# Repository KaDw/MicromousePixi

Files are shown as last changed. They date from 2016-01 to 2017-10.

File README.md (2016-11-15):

# Micromouse Pixi #
	
|  |  |
| ----- | ----- |
| Width | 74mm  |
| Length  | 88mm  |
| Weight  | |
| Wheels  | 3D printed wheels + MZT-302-30 tyres  |
| Microcontroller  | STM32F405RGT6  |
| Motor/Encoder  | Pololu 10:1 HPCB 3000 obr/min + AS5304 encoders  |
| Battery  | Li-Pol Dualsky 7.4V 150mAh 20C  |
| Motor Driver  | TB6612  |
| Sensor | TEFT4300 + SFH4545 X 6  |
| Gyro | FXAS21002C  |

PCB



### Development tools ###

* STM32CubeMX Version 4.17.0
* HAL Libraries - FW_F4 V1.13.1
* Keil uVision 5.21a
* EagleCAD 7.2
* Autodesk Inventor 2016

Development tools can downloaded [here](https://drive.google.com/open?id=0B6SlddUSFtelRTBFR0EwWk1qT1k)

### Setup ###

* CubeMX setup
You can get HAL libraries by going to Help->Install New Libraries->Firmware PAckage for Family STM32F4.
...

### Who do I talk to? ###

* Karol Trzciński 
* Karol Dworakowski karol1dw@gmail.com

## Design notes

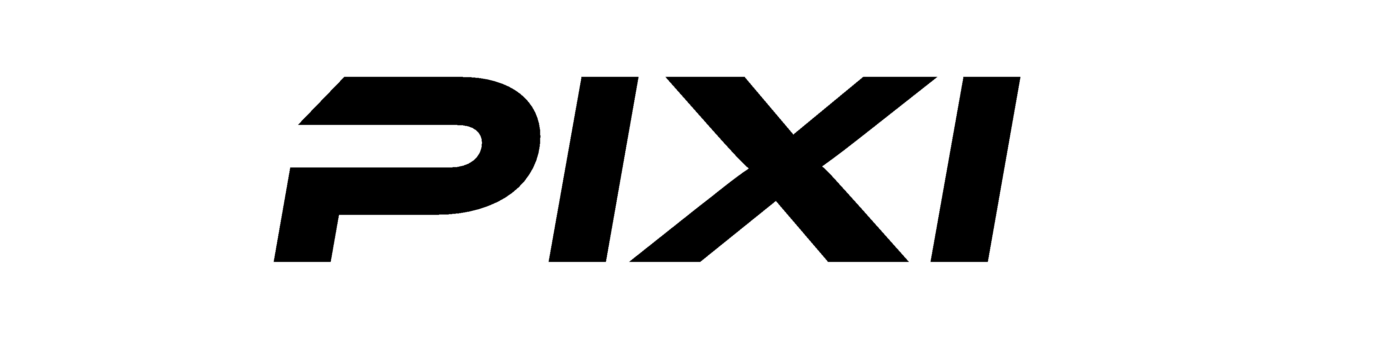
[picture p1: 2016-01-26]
hardware/font/pixi.bmp

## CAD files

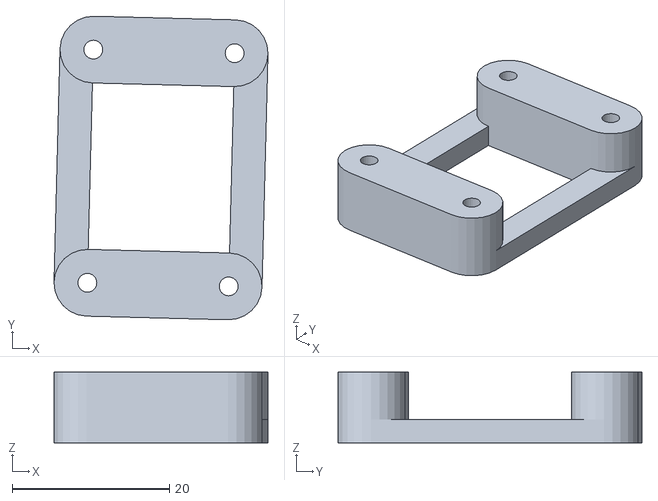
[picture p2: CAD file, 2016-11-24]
hardware/modele/spacer.stl
27.3 x 38.6 x 9.00

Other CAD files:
hardware/modele/wheel.ipt

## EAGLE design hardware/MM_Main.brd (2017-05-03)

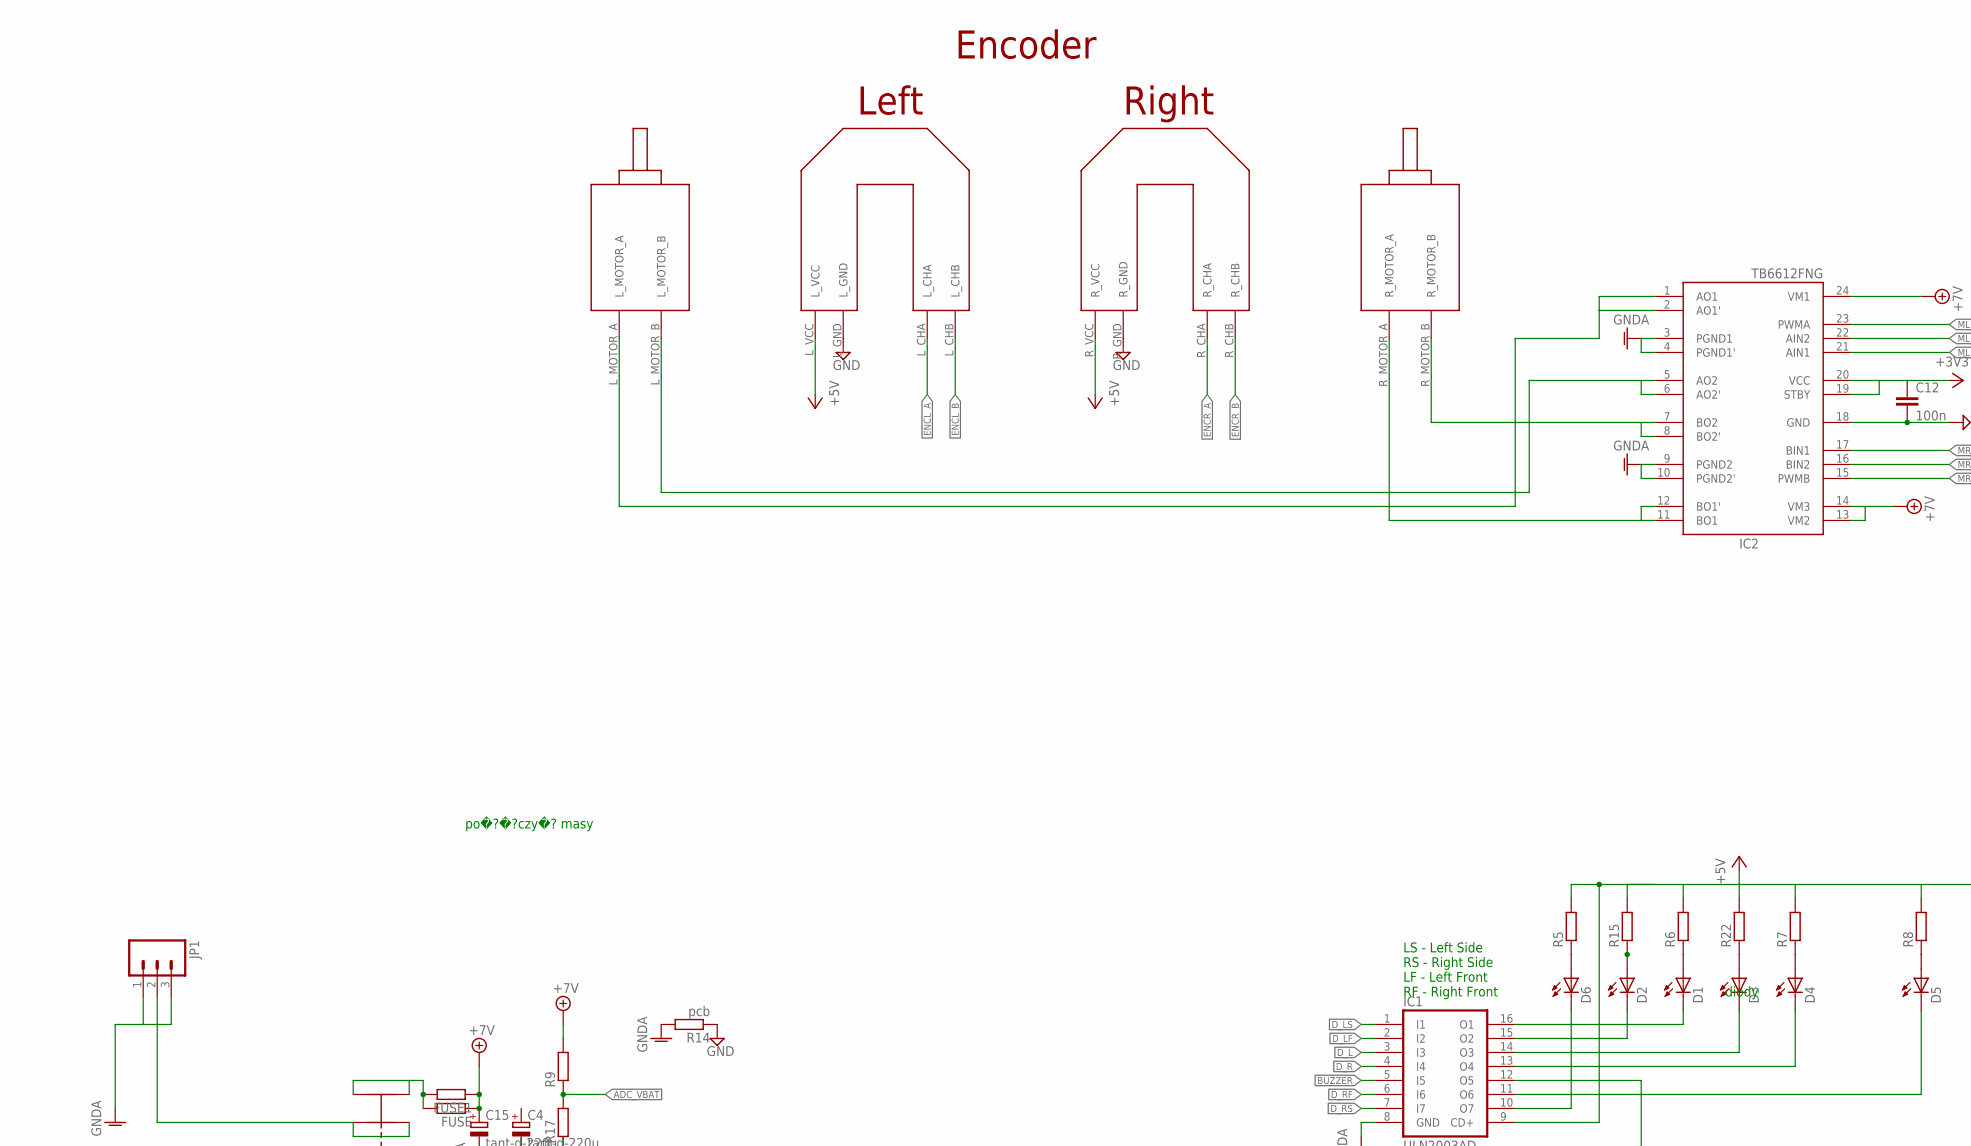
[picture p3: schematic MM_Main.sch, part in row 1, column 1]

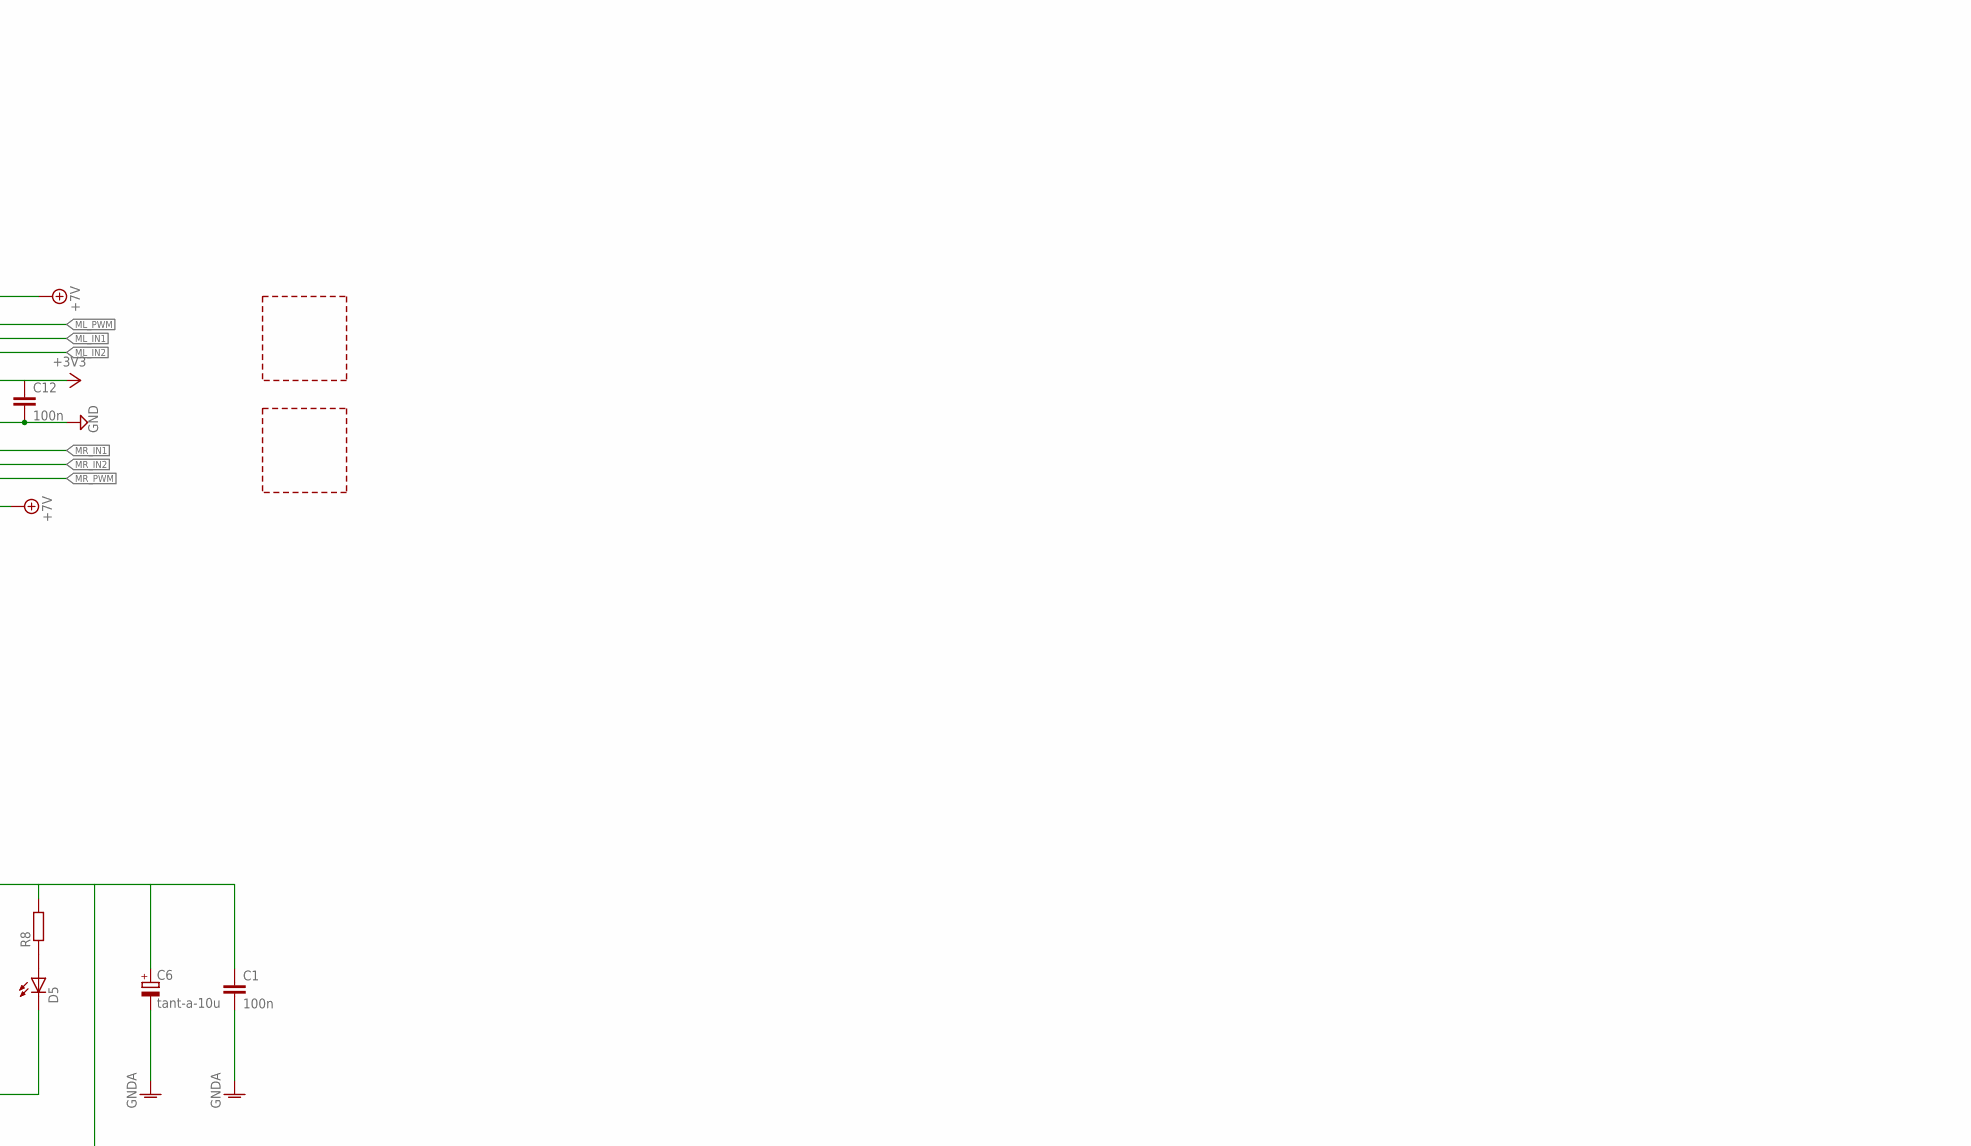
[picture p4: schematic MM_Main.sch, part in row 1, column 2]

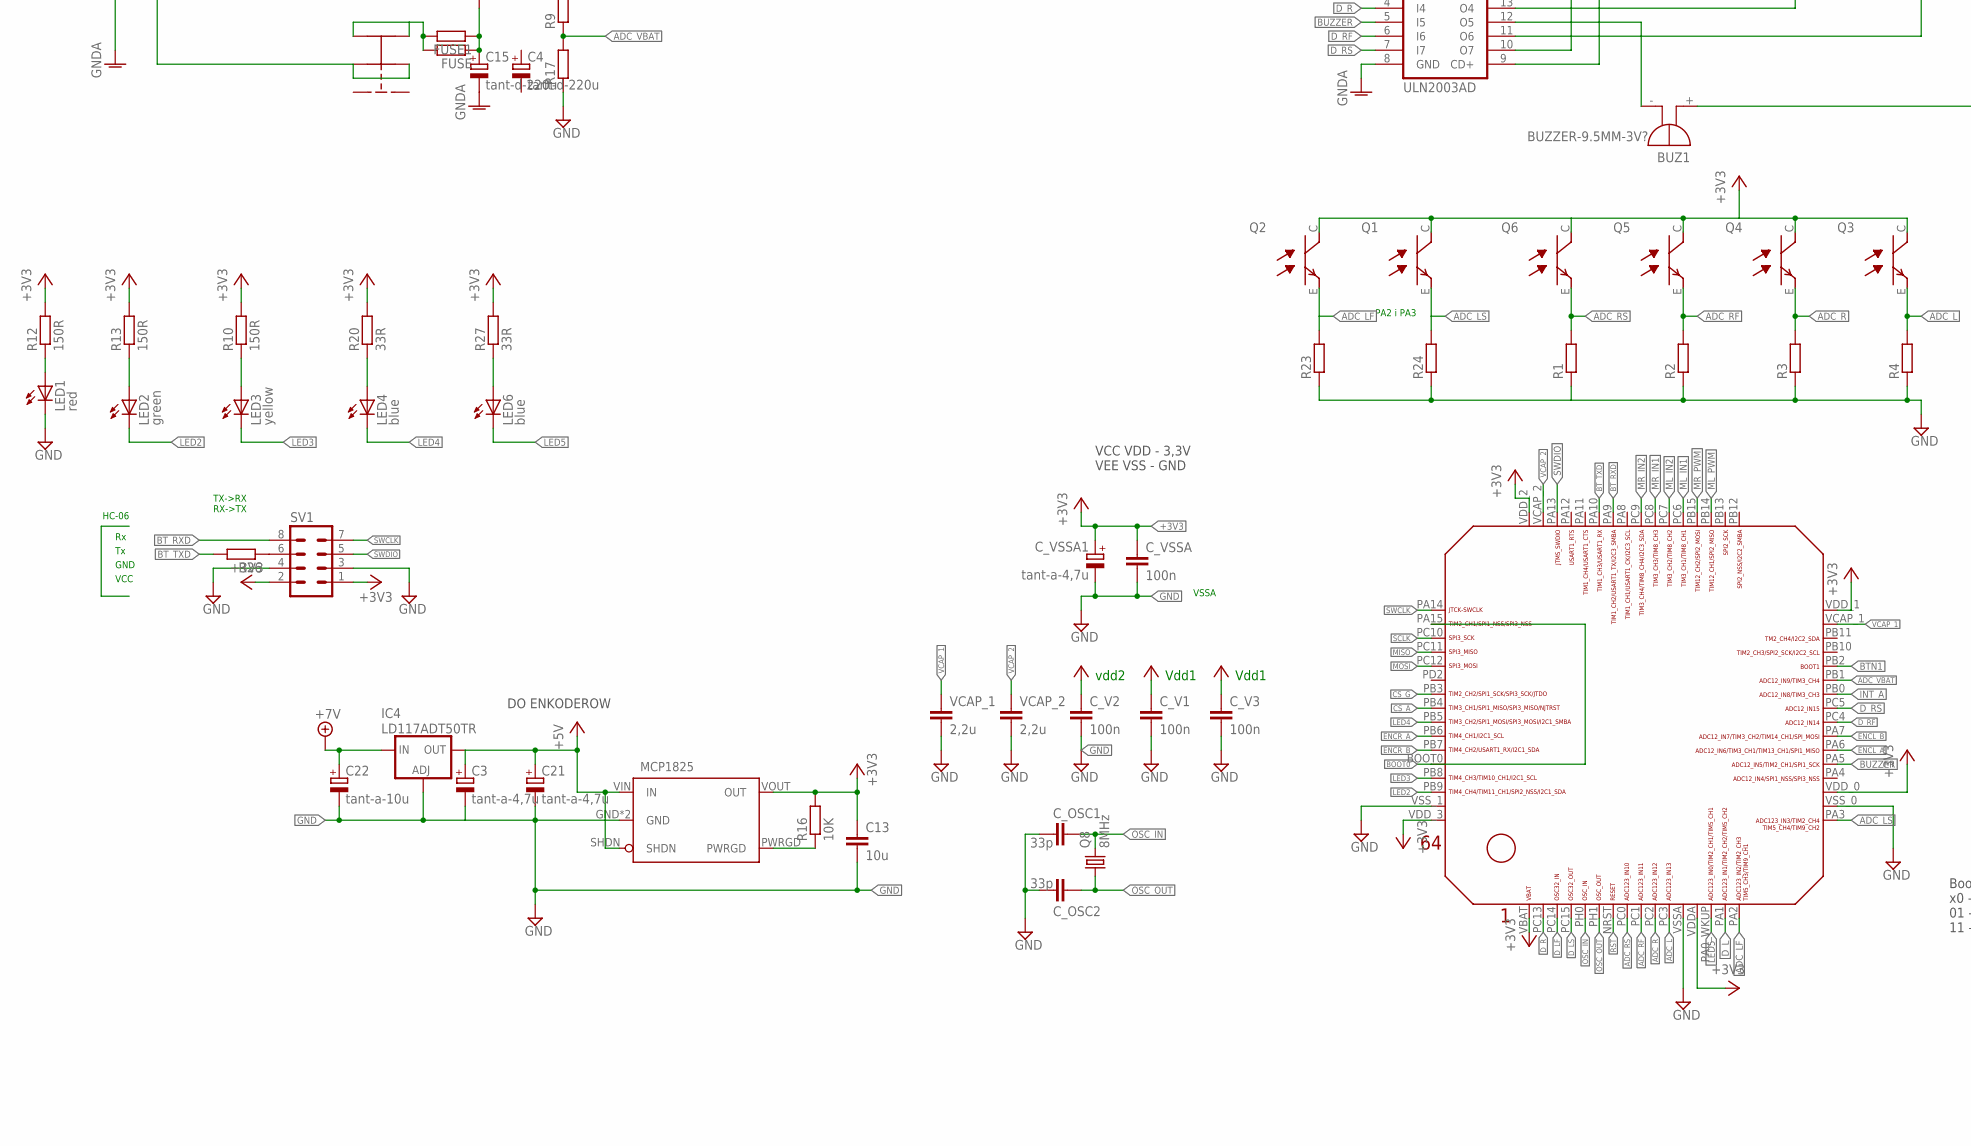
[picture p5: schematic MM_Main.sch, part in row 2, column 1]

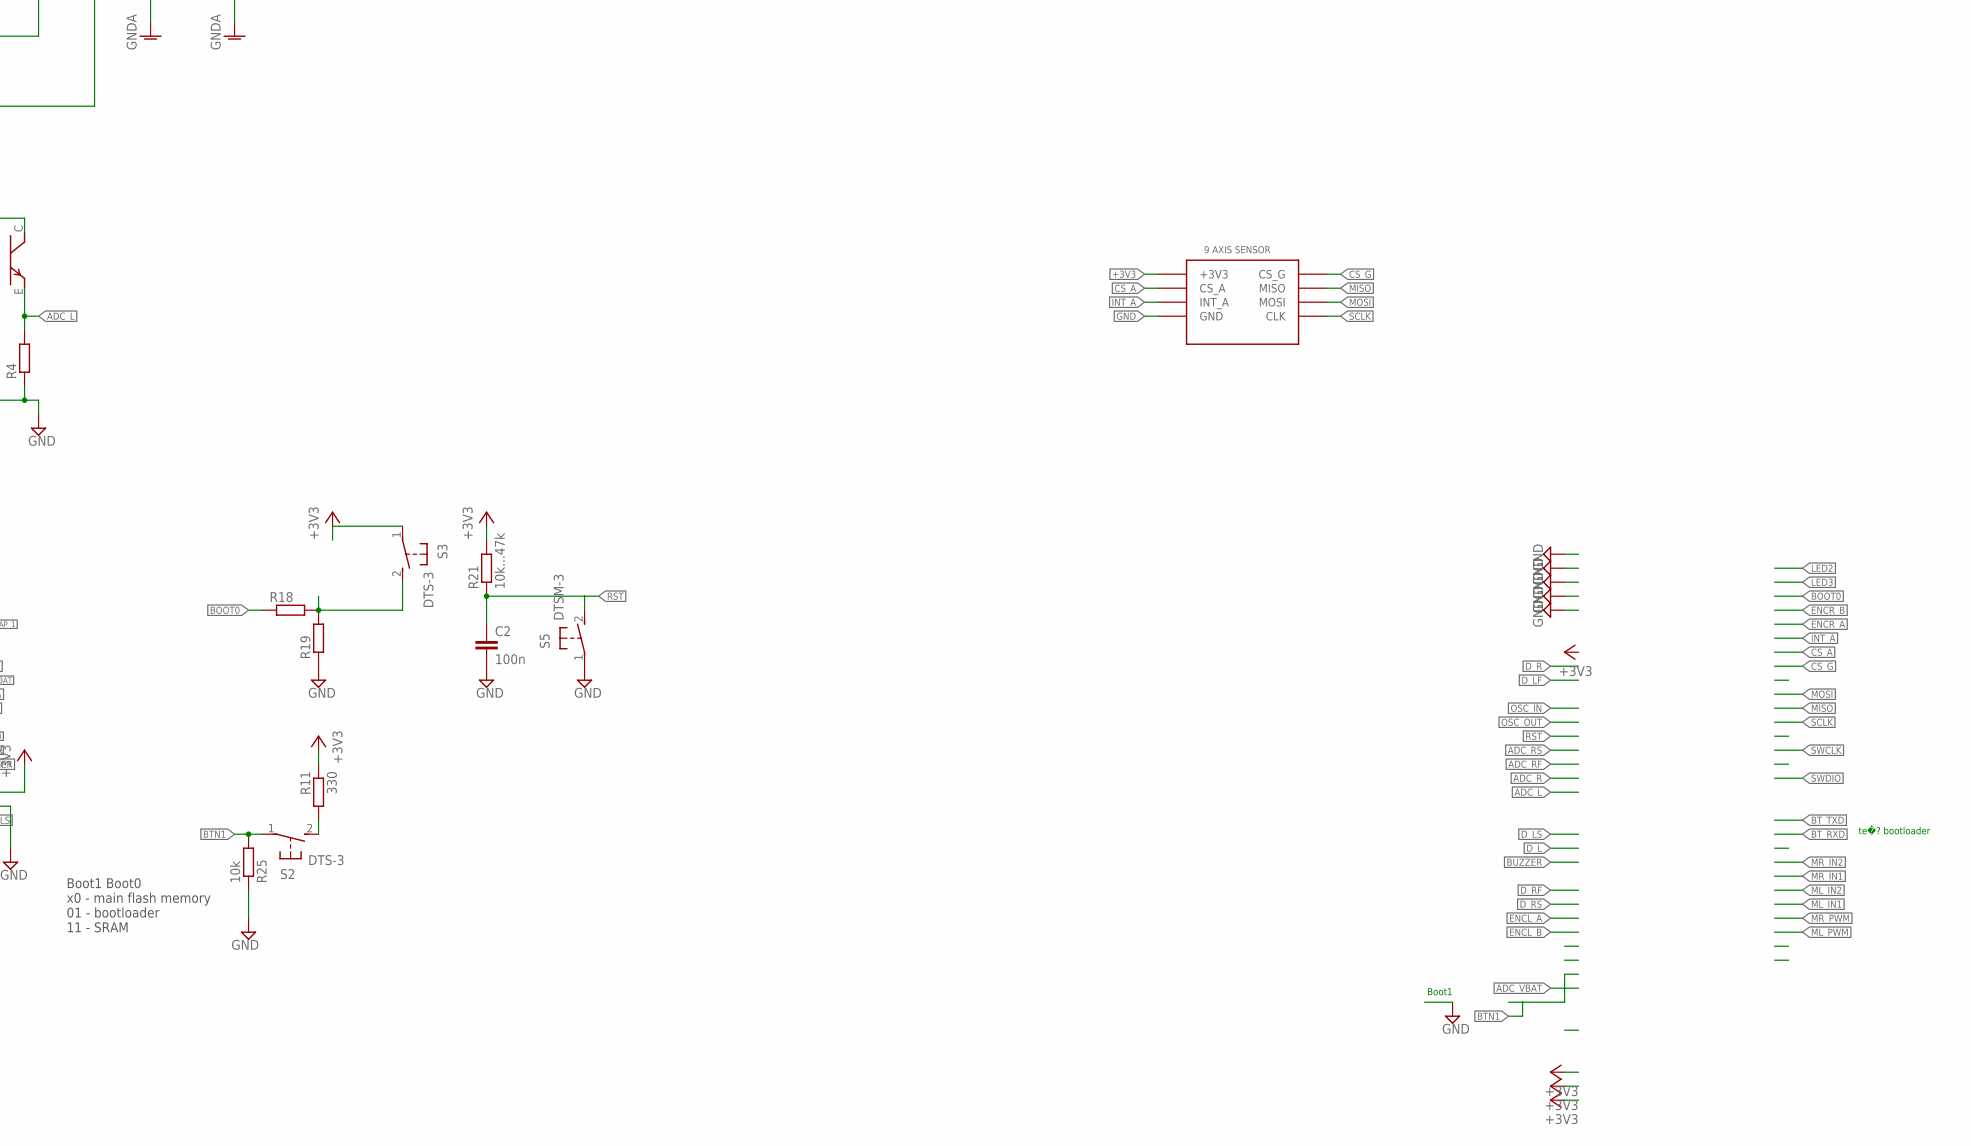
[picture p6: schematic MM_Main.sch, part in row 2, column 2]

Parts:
BUZ1: BUZZER-9.5MM-3V?; BUZZER-9.5MM
C1, C2: 100n; C0805
C3, C21: tant-a-4,7u; SMC_A
C4, C15: tant-d-220u; SMC_D
C6, C22: tant-a-10u; SMC_A
C12: 100n; C0603
C13: 10u; C0805
C_OSC1, C_OSC2: 33p; C0805
C_V1, C_V2, C_V3: 100n; C0805
C_VSSA: 100n; C0805
C_VSSA1: tant-a-4,7u; SMC_A
D1, D2, D3, D4, D5, D6: SFH4545-C
FUSE, FUSE1: R-EU_M3516; M3516
IC1: ULN2003AD; SO16
IC2: TB6612FNG; SSOP24
IC4: LD117ADT50TR; DPACK
IC5: MCP1825; SOT223-5
JP1: M03POLAR; MOLEX-1X3
L1, L2: LABITYNT; LABIRYNT
LED1: red; SML1206
LED2: green; SML1206
LED3: yellow; SML1206
LED4, LED6: blue; SML1206
Q1, Q2, Q3, Q4, Q5, Q6: TEFT4300
Q8: 8MHz; CRYSTAL_5X3.2MM
R1, R2, R3, R4, R5, R6, R7, R8, R9, R15, R17, R18, R19, R22, R23, R24, R26: R-EU_R0805; R0805
R10, R12, R13: 150R; R0805
R11: 330; R0805
R14: pcb; R0201
R16: 10K; R0805
R20, R27: 33R; R0805
R21: 10k...47k; R0805
R25: 10k; R0805
S2, S3: DTS-3
S5: DTSM-3
SV1: MA04-2
U$1: 9AXIS_MODULE; 9AXIS_SENSOR_MODULE
U$3: PRZELACZNIK_SUWAKOWY
U$5: MOTOR_MOUNT
U$6: STM32F4X5; STM32F4-LQFP64
VCAP_1, VCAP_2: 2,2u; C0805

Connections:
+3V3: C12.1, C13.1, C_V1.1, C_V2.1, C_V3.1, C_VSSA.1, C_VSSA1.+, IC2.19 (STBY), IC2.20 (VCC), IC5.VOUT (OUT), Q1.C, Q2.C, Q3.C, Q4.C, Q5.C, Q6.C, R10.2, R11.1, R12.2, R13.2, R16.2, R20.2, R21.2, R27.2, S3.1, SV1.1, SV1.2, U$1.P$1 (+3V3), U$6.VBAT, U$6.VDDA, U$6.VDD_0, U$6.VDD_1, U$6.VDD_2, U$6.VDD_3
+5V: BUZ1.+, C1.1, C3.+, C6.+, C21.+, IC1.9 (CD+), IC4.4 (OUT), IC5.SHDN, IC5.VIN (IN), R5.2, R6.2, R7.2, R8.2, R15.2, R22.2, U$5.L_VCC, U$5.R_VCC
+7V: C15.+, C22.+, FUSE.1, FUSE1.1, IC2.13 (VM2), IC2.14 (VM3), IC2.24 (VM1), IC4.3 (IN), R9.2
ADC_L: Q3.E, R4.2, U$6.PC3
ADC_LF: Q2.E, R23.2, U$6.PA2
ADC_LS: Q1.E, R24.2, U$6.PA3
ADC_R: Q4.E, R3.2, U$6.PC2
ADC_RF: Q5.E, R2.2, U$6.PC1
ADC_RS: Q6.E, R1.2, U$6.PC0
ADC_VBAT: R9.1, R17.2, U$6.PB1
BOOT0: R18.1, U$6.BOOT0, U$6.PA15
BTN1: R25.2, S2.1, U$6.PB2
BT_RXD: SV1.8, U$6.PA9
BT_TXD: R26.2, U$6.PA10
BUZZER: IC1.5 (I5), U$6.PA5
CS_A: U$1.P$2 (CS_A), U$6.PB4
CS_G: U$1.P$8 (CS_G), U$6.PB3
D_L: IC1.3 (I3), U$6.PA1
D_LF: IC1.2 (I2), U$6.PC14
D_LS: IC1.1 (I1), U$6.PC15
D_R: IC1.4 (I4), U$6.PC13
D_RF: IC1.6 (I6), U$6.PC4
D_RS: IC1.7 (I7), U$6.PC5
ENCL_A: U$5.L_CHA, U$6.PA6
ENCL_B: U$5.L_CHB, U$6.PA7
ENCR_A: U$5.R_CHA, U$6.PB6
ENCR_B: U$5.R_CHB, U$6.PB7
GND: C2.2, C3.-, C12.2, C13.2, C21.-, C22.-, C_OSC1.1, C_OSC2.1, C_V1.2, C_V2.2, C_V3.2, C_VSSA.2, C_VSSA1.-, IC2.18 (GND), IC4.1 (ADJ), IC5.GND, IC5.GND_TAB (GND), LED1.C, R1.1, R2.1, R3.1, R4.1, R14.1, R17.1, R19.1, R23.1, R24.1, R25.1, S5.1, SV1.3, SV1.4, U$1.P$4 (GND), U$5.L_GND, U$5.R_GND, U$6.VSSA, U$6.VSS_0, U$6.VSS_1, VCAP_1.2, VCAP_2.2
GNDA: C1.2, C6.-, C15.-, IC1.8 (GND), IC2.3 (PGND1), IC2.4 (PGND1'), IC2.9 (PGND2), IC2.10 (PGND2'), JP1.1, JP1.3, R14.2
INT_A: U$1.P$3 (INT_A), U$6.PB0
LED2: LED2.C, U$6.PB9
LED3: LED3.C, U$6.PB8
LED4: LED4.C, U$6.PB5
LED5: LED6.C, U$6.PA0_WKUP (PA0_AKUP)
MISO: U$1.P$7 (MISO), U$6.PC11
ML_IN1: IC2.22 (AIN2), U$6.PC6
ML_IN2: IC2.21 (AIN1), U$6.PC7
ML_PWM: IC2.23 (PWMA), U$6.PB14
MOSI: U$1.P$6 (MOSI), U$6.PC12
MR_IN1: IC2.17 (BIN1), U$6.PC8
MR_IN2: IC2.16 (BIN2), U$6.PC9
MR_PWM: IC2.15 (PWMB), U$6.PB15
unnamed: IC5.PWRGD, R16.1
unnamed: D2.ANODA (A), R15.1
unnamed: D6.ANODA (A), R5.1
unnamed: IC2.7 (BO2), IC2.8 (BO2'), U$5.R_MOTOR_B
unnamed: IC2.11 (BO1), IC2.12 (BO1'), U$5.R_MOTOR_A
unnamed: IC2.1 (AO1), IC2.2 (AO1'), U$5.L_MOTOR_A
unnamed: LED3.A, R10.1
unnamed: D1.ANODA (A), R6.1
unnamed: D4.ANODA (A), R7.1
unnamed: D5.ANODA (A), R8.1
unnamed: LED1.A, R12.1
unnamed: IC2.5 (AO2), IC2.6 (AO2'), U$5.L_MOTOR_B
unnamed: BUZ1.-, IC1.12 (O5)
unnamed: D3.ANODA (A), R22.1
unnamed: LED2.A, R13.1
unnamed: LED4.A, R20.1
unnamed: R18.2, R19.2, S3.2
unnamed: FUSE.2, FUSE1.2, U$3.3, U$3.6
unnamed: R26.1, SV1.6
unnamed: R11.2, S2.2
unnamed: LED6.A, R27.1
unnamed: JP1.2, U$3.2, U$3.5
OSC_IN: C_OSC1.2, Q8.P$2 (2), U$6.PH0
OSC_OUT: C_OSC2.2, Q8.P$1 (1), U$6.PH1
RST: C2.1, R21.1, S5.2, U$6.NRST
SCLK: U$1.P$5 (CLK), U$6.PC10
SENSOR_L: D3.KATODA (C), IC1.14 (O3)
SENSOR_LF: D2.KATODA (C), IC1.15 (O2)
SENSOR_LS: D1.KATODA (C), IC1.16 (O1)
SENSOR_R: D4.KATODA (C), IC1.13 (O4)
SENSOR_RF: D5.KATODA (C), IC1.11 (O6)
SENSOR_RS: D6.KATODA (C), IC1.10 (O7)
SWCLK: SV1.7, U$6.PA14
SWDIO: SV1.5, U$6.PA13
VCAP_1: U$6.VCAP_1, VCAP_1.1
VCAP_2: U$6.VCAP_2, VCAP_2.1

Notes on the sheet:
diody
Boot1 Boot0 x0 - main flash memory 01 - bootloader 11 - SRAM
DO ENKODEROW
te�? bootloader
Boot1
VSSA
po�?�?czy�? masy
Vdd1
vdd2
VCC VDD - 3,3V VEE VSS - GND
TX->RX RX->TX
PA2 i PA3
GND
VCC
HC-06
LS - Left Side RS - Right Side LF - Left Front RF - Right Front

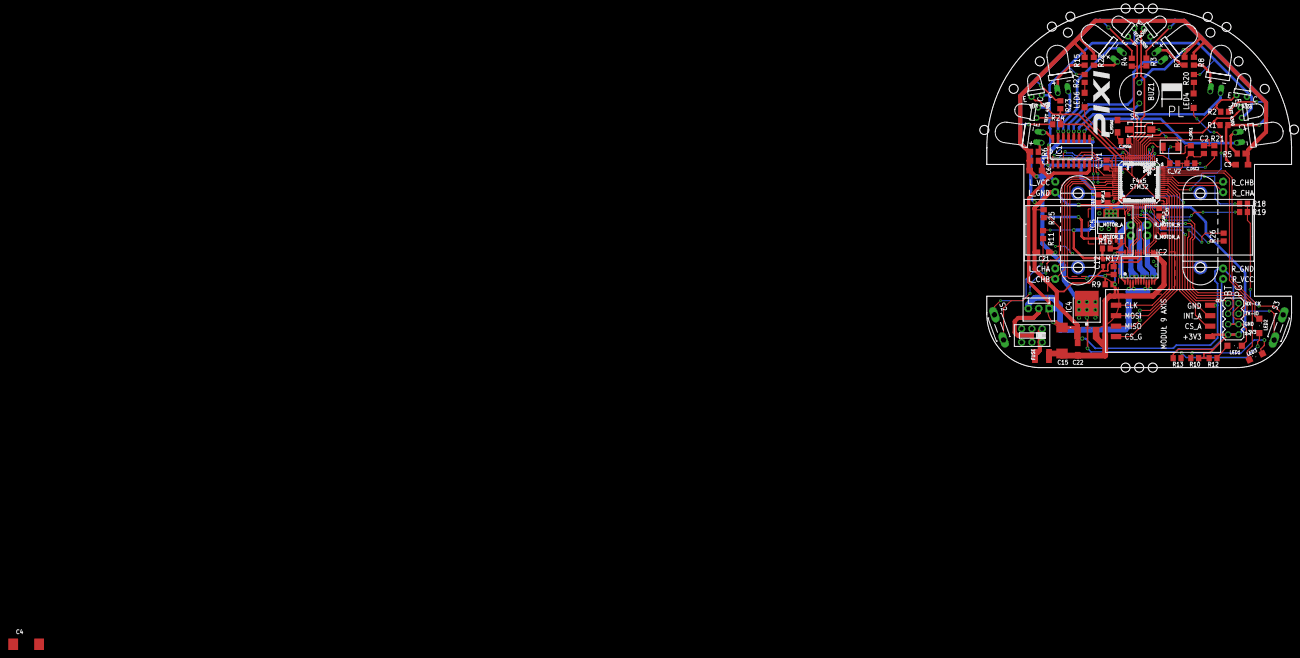
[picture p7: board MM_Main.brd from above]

Board: 2 copper layers, 74.0 x 87.2 mm, 82 parts (0 on the bottom side), 78 nets.

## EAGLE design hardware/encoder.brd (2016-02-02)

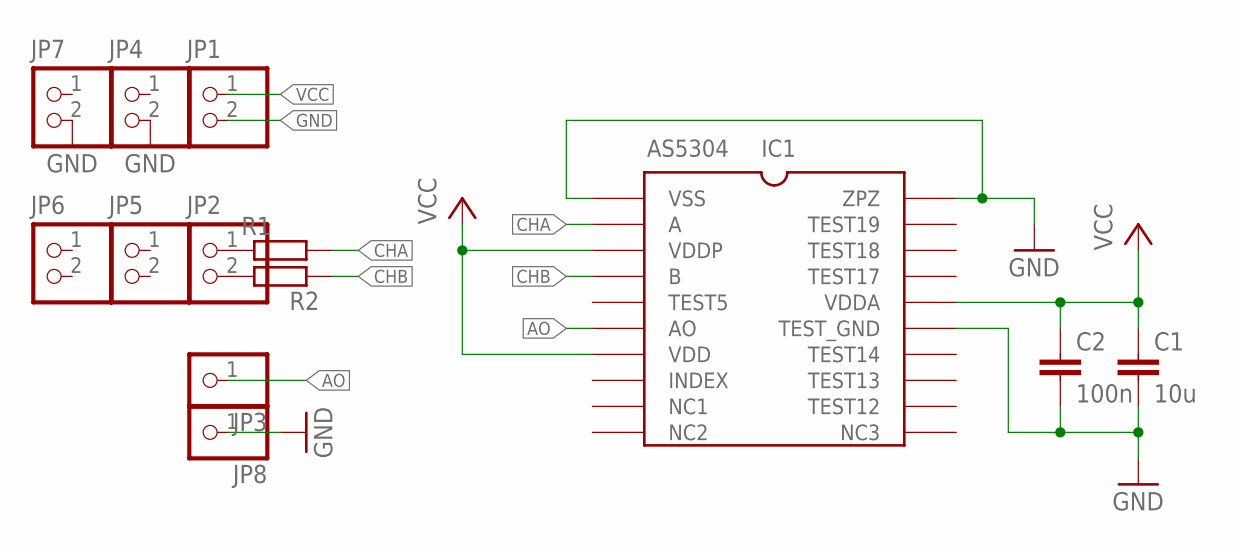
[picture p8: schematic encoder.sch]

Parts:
C1: 10u; C0603
C2: 100n; C0603
IC1: AS5304; TSSOP20
JP1, JP2, JP4, JP5, JP6, JP7: PINHD_1X2_ROUND
JP3, JP8: PINHD-1X1; 1X01
R1, R2: R-EU_R0805; R0805

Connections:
AO: IC1.AO, JP3.1
CHA: IC1.A, R1.2
CHB: IC1.B, R2.1
GND: C1.2, C2.2, IC1.TEST_GND, IC1.VSS, IC1.ZPZ, JP1.2, JP4.2, JP7.2, JP8.1
unnamed: JP2.1, R1.1
unnamed: JP2.2, R2.2
VCC: C1.1, C2.1, IC1.VDD, IC1.VDDA, IC1.VDDP, JP1.1

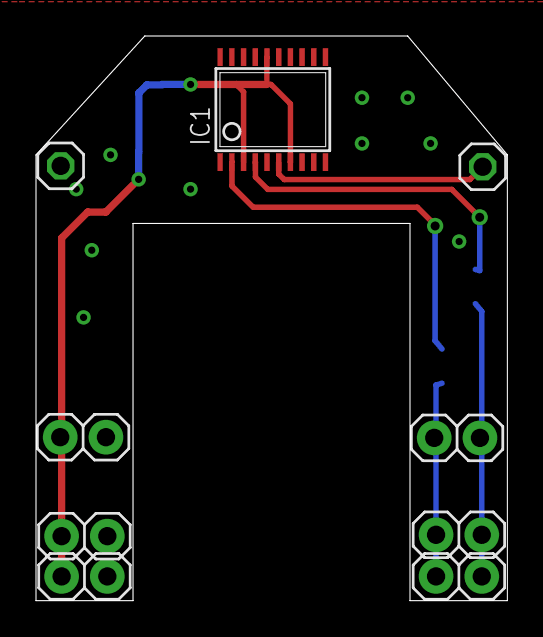
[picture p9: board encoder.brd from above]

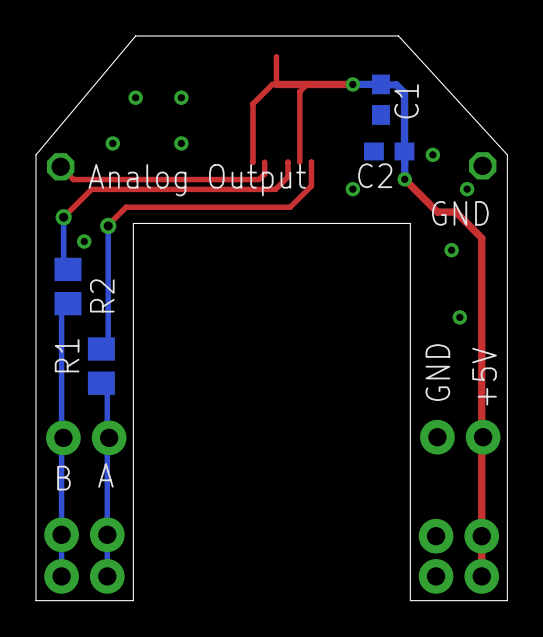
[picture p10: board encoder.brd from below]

Board: 2 copper layers, 26.2 x 31.4 mm, 13 parts (4 on the bottom side), 7 nets.

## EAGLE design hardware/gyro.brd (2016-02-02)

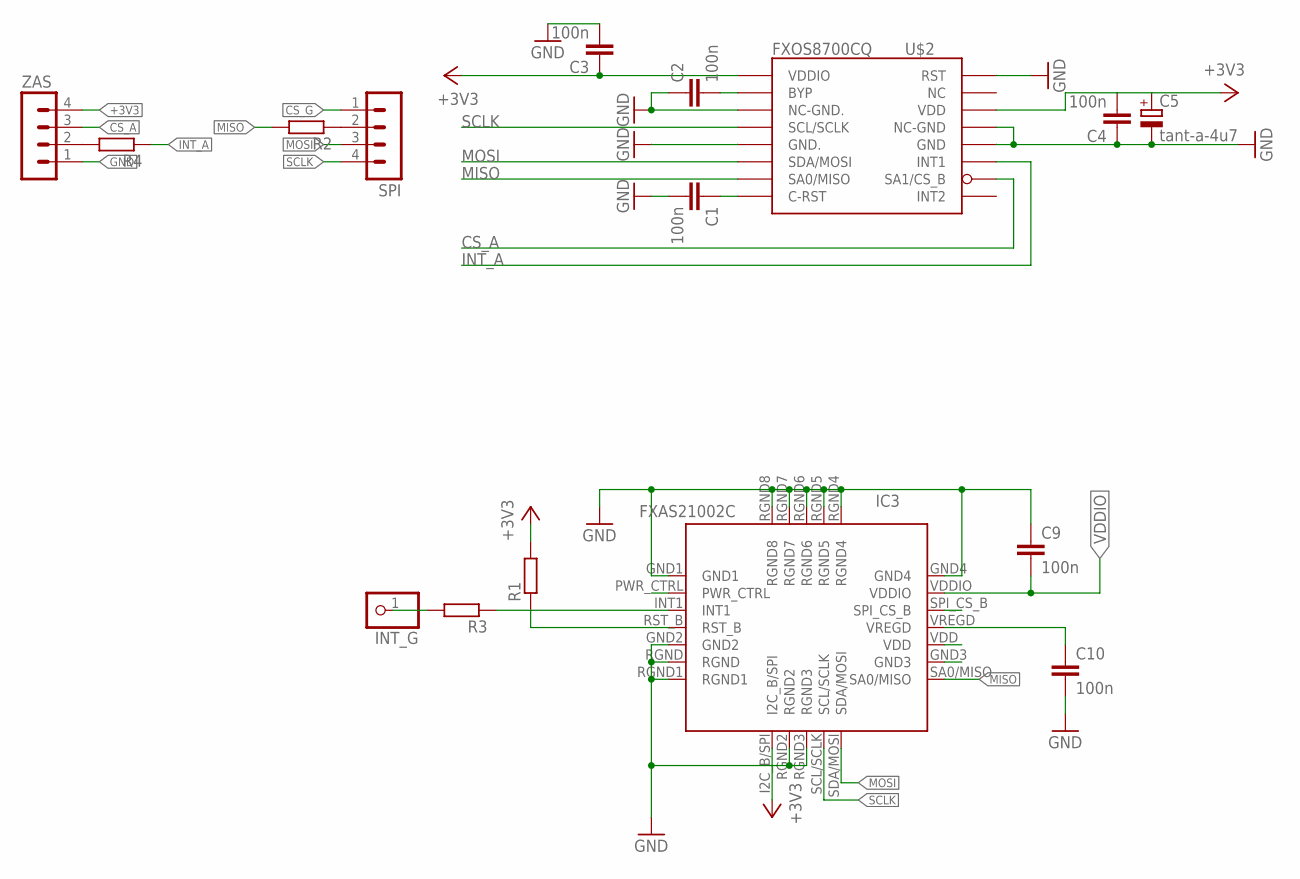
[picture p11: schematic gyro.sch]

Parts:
C1, C2, C3, C4, C9, C10: 100n; C0603
C5: tant-a-4u7; SMC_A
IC3: FXAS21002C; QFN24-4X4
INT_G: PINHD-1X1; 1X01
R1, R2, R3, R4: R-EU_R0603; R0603
SPI: MA04-1
U$2: FXOS8700CQR1; QFN16-5X3
ZAS: MA04-1

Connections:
+3V3: C3.1, C4.2, C5.+, IC3.I2C_B/SPI, IC3.VDD, R1.2, U$2.P$1 (VDDIO), U$2.P$14 (VDD), ZAS.4
CS_A: U$2.P$10 (SA1/CS_B), ZAS.3
CS_G: IC3.SPI_CS_B, SPI.1
GND: C1.2, C2.1, C3.2, C4.1, C5.-, C9.1, C10.2, IC3.GND1, IC3.GND2, IC3.GND3, IC3.GND4, IC3.RGND, IC3.RGND1, IC3.RGND2, IC3.RGND3, IC3.RGND4, IC3.RGND5, IC3.RGND6, IC3.RGND7, IC3.RGND8, U$2.P$3 (NC-GND.), U$2.P$5 (GND.), U$2.P$12 (GND), U$2.P$13 (NC-GND), U$2.P$16 (RST), ZAS.1
INT_A: R4.1, U$2.P$11 (INT1)
MISO: IC3.SA0/MISO, R2.2, U$2.P$7 (SA0/MISO)
MOSI: IC3.SDA/MOSI, SPI.3, U$2.P$6 (SDA/MOSI)
unnamed: R2.1, SPI.2
unnamed: INT_G.1, R3.2
unnamed: IC3.INT1, R3.1
unnamed: R4.2, ZAS.2
unnamed: C1.1, U$2.P$8 (C-RST)
unnamed: C2.2, U$2.P$2 (BYP)
unnamed: C10.1, IC3.VREGD
unnamed: IC3.RST_B, R1.1
SCLK: IC3.SCL/SCLK, SPI.4, U$2.P$4 (SCL/SCLK)
VDDIO: C9.2, IC3.VDDIO

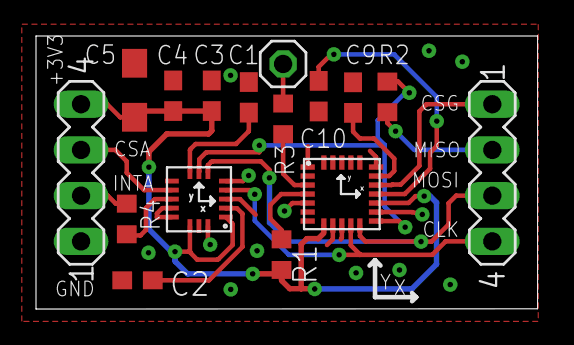
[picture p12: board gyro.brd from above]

Board: 2 copper layers, 27.9 x 15.2 mm, 16 parts (0 on the bottom side), 17 nets.

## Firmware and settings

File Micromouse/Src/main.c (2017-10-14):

/**
  ******************************************************************************
  * File Name          : main.c
  * Description        : Main program body
  ******************************************************************************
  *
  * COPYRIGHT(c) 2016 STMicroelectronics
  *
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
  ******************************************************************************
  */
/* Includes ------------------------------------------------------------------*/
#include "main.h"
#include "stm32f4xx_hal.h"
#include "adc.h"
#include "dma.h"
#include "spi.h"
#include "tim.h"
#include "usart.h"
#include "gpio.h"

/* USER CODE BEGIN Includes */
#include "gpio_r.h"
#include "sensor.h"
#include "fxas21002c.h"
#include "motor.h"
#include "UI.h"
#include "queue.h"
/* USER CODE END Includes */


/* USER CODE BEGIN PV */
//char Rx_buf[100];
//char Tx_buf[50];
/* ADC */

/* USER CODE END PV */

void SystemClock_Config(void);
void Error_Handler(void);

/* USER CODE BEGIN PFP */
/* USER CODE END PFP */

int main(void)
{

  /* MCU Configuration----------------------------------------------------------*/

  /* Reset of all peripherals, Initializes the Flash interface and the Systick. */
  HAL_Init();

  /* Configure the system clock */
  SystemClock_Config();

  /* Initialize all configured peripherals */
  MX_GPIO_Init();
  MX_DMA_Init();
  MX_ADC1_Init();
  MX_SPI3_Init();
  MX_TIM3_Init();
  MX_TIM4_Init();
  MX_TIM12_Init();
  MX_USART1_UART_Init();
  MX_TIM6_Init();
  MX_TIM1_Init();
  MX_TIM2_Init();

  /* USER CODE BEGIN 2 */
	MotorInit();
  UI_Init();
	GyroInit();
	GyroCalibrate(0.001, 100);
	HAL_UART_Receive_DMA(&huart1, (uint8_t*)Rx_buf, 1);
	//HAL_TIM_Base_Start_IT(&htim6);
  /* USER CODE END 2 */

  /* Infinite loop */
  /* USER CODE BEGIN WHILE */
	//ENABLE_GYRO();
	//SensorOff();
	ENABLE_ENCODER;
	ENABLE_SENSOR;
	UI_LedOn(UI_LED_GREEN);
	UI_WaitBtnL();
	UI_LedOffAll();
	HAL_Delay(2000);
	q_push(&queue, MotorGoA, 180, 180, 100);
	q_push(&queue, MotorGoA, 200, 200, 100);
//	q_push(&queue, MotorGoA, 200, 200, 100);
//	q_push(&queue, MotorGoA, 200, 200, 100);
	q_push(&queue, MotorTurnA, 90, 0, 100);
//	q_push(&queue, MotorGoA, 100, 100, 100);
//	q_push(&queue, MotorTurnA, 90, 0, 100);
	q_push(&queue, MotorGoA, 200, 200, 100);
	//ADCreadAmbient();
	
	MotorGoA(37, 37, 200);
//	MotorTurnA(180, 0, 250);
//	MotorGoA(180, 180, 200);
//	MotorTurnA(-180, 0, 250);
//	MotorGoA(200, 200, 250);
	HAL_TIM_Base_Start_IT(&htim6);
	while (1)
	{
  /* USER CODE END WHILE */
//		if(distance[5] < 60)
//			MotorGo(500, 500, 200);
//		HAL_Delay(3000);
  /* USER CODE BEGIN 3 */
	}

  /* USER CODE END 3 */

}

/** System Clock Configuration
*/
void SystemClock_Config(void)
{

  RCC_OscInitTypeDef RCC_OscInitStruct;
  RCC_ClkInitTypeDef RCC_ClkInitStruct;

    /**Configure the main internal regulator output voltage 
    */
  __HAL_RCC_PWR_CLK_ENABLE();

  __HAL_PWR_VOLTAGESCALING_CONFIG(PWR_REGULATOR_VOLTAGE_SCALE1);

    /**Initializes the CPU, AHB and APB busses clocks 
    */
  RCC_OscInitStruct.OscillatorType = RCC_OSCILLATORTYPE_HSE;
  RCC_OscInitStruct.HSEState = RCC_HSE_ON;
  RCC_OscInitStruct.PLL.PLLState = RCC_PLL_ON;
  RCC_OscInitStruct.PLL.PLLSource = RCC_PLLSOURCE_HSE;
  RCC_OscInitStruct.PLL.PLLM = 4;
  RCC_OscInitStruct.PLL.PLLN = 168;
  RCC_OscInitStruct.PLL.PLLP = RCC_PLLP_DIV2;
  RCC_OscInitStruct.PLL.PLLQ = 4;
  if (HAL_RCC_OscConfig(&RCC_OscInitStruct) != HAL_OK)
  {
    Error_Handler();
  }

    /**Initializes the CPU, AHB and APB busses clocks 
    */
  RCC_ClkInitStruct.ClockType = RCC_CLOCKTYPE_HCLK|RCC_CLOCKTYPE_SYSCLK
                              |RCC_CLOCKTYPE_PCLK1|RCC_CLOCKTYPE_PCLK2;
  RCC_ClkInitStruct.SYSCLKSource = RCC_SYSCLKSOURCE_PLLCLK;
  RCC_ClkInitStruct.AHBCLKDivider = RCC_SYSCLK_DIV1;
  RCC_ClkInitStruct.APB1CLKDivider = RCC_HCLK_DIV4;
  RCC_ClkInitStruct.APB2CLKDivider = RCC_HCLK_DIV2;

  if (HAL_RCC_ClockConfig(&RCC_ClkInitStruct, FLASH_LATENCY_5) != HAL_OK)
  {
    Error_Handler();
  }

    /**Configure the Systick interrupt time 
    */
  HAL_SYSTICK_Config(HAL_RCC_GetHCLKFreq()/1000);

    /**Configure the Systick 
    */
  HAL_SYSTICK_CLKSourceConfig(SYSTICK_CLKSOURCE_HCLK);

  /* SysTick_IRQn interrupt configuration */
  HAL_NVIC_SetPriority(SysTick_IRQn, 0, 0);
}

/* USER CODE BEGIN 4 */
//void HAL_SYSTICK_Callback(){

//}


// Bluetooth manual mode
void HAL_UART_RxCpltCallback(UART_HandleTypeDef *huart){
	extern float Kp, Ki, Kd;
	if('a' <= *Rx_buf && *Rx_buf <= 'z')
		*Rx_buf += 'A'-'a';
	
	switch(*Rx_buf){
		case 'W':
		case 'F':
			MotorGoA(300, 300, 200);
		break;
		
		case 'S':
			MotorGoA(-300, -300, 200);
		break;
		
		case 'D':
		//case 'R': 
			MotorTurnA(45, 33, 200);
		break;
			
		case 'A':
		//case 'L':
			MotorTurnA(-45, 33, 200);
		break;
		
		case 'Z':
			MotorStop();
		break;
		
		case 'Q':
			MotorGoA(300, 300, 100);
		break;
		case 'E':
			MotorGoA(300, 300, 300);
		break;
		case 'R':
			MotorGoA(300, 300, 400);
		break;
		
		case 'P':
			Kp += 0.5f;
		break;
		case 'L':
			Kp -= 0.5f;
		
		case 'I':
			Ki += 0.02f;
		break;
		case 'J':
			Ki -= 0.02f;
		break;
		
		case 'Y':
			Kd += 0.01f;
		break;
		case 'G':
			Kd -= 0.01f;
		break;
		}
	
		if(*Rx_buf == 'Y' || *Rx_buf == 'G')
		{
			char * ptr = Tx_buf;
			ptr = strcpy(ptr, "Kp:");
			ptr = _ftoa(Kp, ptr, 2);
			ptr = strcpy(ptr, " Ki: ");
			ptr = _ftoa(Ki, ptr, 2);
			ptr = strcpy(ptr, " Kd: ");
			ptr = _ftoa(Kd, ptr, 2);
			HAL_UART_Transmit_DMA(&huart1, (uint8_t*)Tx_buf, ptr-Tx_buf);
		}
}

/* USER CODE END 4 */
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


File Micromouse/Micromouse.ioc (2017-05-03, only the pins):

Mcu.UserName=STM32F405RGTx
PA0-WKUP.GPIO_Label=LED4
PA0-WKUP.Signal=GPIO_Output
PA1.GPIO_Label=D_L
PA1.Signal=GPIO_Output
PA10.GPIO_Label=BT_RX
PA10.Signal=USART1_RX
PA13.Signal=SYS_JTMS-SWDIO
PA14.Signal=SYS_JTCK-SWCLK
PA15.GPIO_Label=BTN2
PA15.Signal=GPXTI15
PA2.GPIO_Label=ADC_LF
PA2.Signal=ADCx_IN2
PA3.GPIO_Label=ADC_LS
PA3.Signal=ADCx_IN3
PA5.GPIO_Label=BUZZER
PA5.Signal=S_TIM2_CH1_ETR
PA6.GPIO_Label=ENCL_A
PA6.Signal=S_TIM3_CH1
PA7.GPIO_Label=ENCL_B
PA7.Signal=S_TIM3_CH2
PA9.GPIO_Label=BT_TX
PA9.Signal=USART1_TX
PB0.GPIO_Label=INT_G
PB0.Signal=GPXTI0
PB1.GPIO_Label=ADC_VBAT
PB1.Signal=ADCx_IN9
PB14.GPIO_Label=ML_PWM
PB14.Signal=S_TIM12_CH1
PB15.GPIO_Label=MR_PWM
PB15.Signal=S_TIM12_CH2
PB2.GPIO_Label=BTN
PB2.Signal=GPXTI2
PB3.GPIO_Label=CS_G
PB3.Signal=GPIO_Output
PB4.GPIO_Label=CS_A
PB4.Signal=GPIO_Output
PB5.GPIO_Label=LED3
PB5.Signal=GPIO_Output
PB6.GPIO_Label=ENCR_A
PB6.Signal=S_TIM4_CH1
PB7.GPIO_Label=ENCR_B
PB7.Signal=S_TIM4_CH2
PB8.GPIO_Label=LED2
PB8.Signal=GPIO_Output
PB9.GPIO_Label=LED1
PB9.Signal=GPIO_Output
PC0.GPIO_Label=ADC_RS
PC0.Signal=ADCx_IN10
PC1.GPIO_Label=ADC_RF
PC1.Signal=ADCx_IN11
PC10.Signal=SPI3_SCK
PC11.Signal=SPI3_MISO
PC12.Signal=SPI3_MOSI
PC13-ANTI_TAMP.GPIO_Label=D_R
PC13-ANTI_TAMP.Signal=GPIO_Output
PC14-OSC32_IN.GPIO_Label=D_LF
PC14-OSC32_IN.Signal=GPIO_Output
PC15-OSC32_OUT.GPIO_Label=D_LS
PC15-OSC32_OUT.Signal=GPIO_Output
PC2.GPIO_Label=ADC_R
PC2.Signal=ADCx_IN12
PC3.GPIO_Label=ADC_L
PC3.Signal=ADCx_IN13
PC4.GPIO_Label=D_RF
PC4.Signal=GPIO_Output
PC5.GPIO_Label=D_RS
PC5.Signal=GPIO_Output
PC6.GPIO_Label=ML_IN1
PC6.Signal=GPIO_Output
PC7.GPIO_Label=ML_IN2
PC7.Signal=GPIO_Output
PC8.GPIO_Label=MR_IN1
PC8.Signal=GPIO_Output
PC9.GPIO_Label=MR_IN2
PC9.Signal=GPIO_Output
PH0-OSC_IN.Signal=RCC_OSC_IN
PH1-OSC_OUT.Signal=RCC_OSC_OUT

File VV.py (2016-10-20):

# -*- coding: utf-8 -*-

import math
import matplotlib.pyplot as pl

MOTOR_ACC_V = 1000
MOTOR_DRIVER_T = 0.001

class motors_t:
    def __init__(self):
        self.mot0 = 0 #dest vel float
        self.mot1 = 0
        self.cmot0 = 0 #current vel float
        self.cmot1 = 0
        self.time = 0
        self.previousV = 0.0

#error CalcTime(487,-2003, 9999999999)


def MotorCalcTime(lastV, s, vel): #float float float
    if(vel == 0): #change
        return 0
    Tacc = abs(vel-lastV)/MOTOR_ACC_V #float, use fabs()
    Sacc = (lastV+vel)*0.5*Tacc #float
    Tcon = abs((s-Sacc)/vel) #floats
    T = 0 #float
    if(abs(Sacc) > abs(s)): #fabs
        # gdy tylko przyspieszamy, to czas jest opisany zaleznoscia
        # s = a*t*t/2 + v0*t #change ten wzor jest dobry
        print("Time - part")
        s = abs(s) #fabs #change
        T = (-lastV + math.sqrt(lastV*lastV+2*s*MOTOR_ACC_V))/MOTOR_ACC_V #liczba pod pierwistkiem jest dodatnia
        if(T < 0):
            T = (lastV + math.sqrt(lastV*lastV+2*s*MOTOR_ACC_V))/MOTOR_ACC_V
    else: #change
        # gdy przyspieszamy oraz poruszamy sie ze stala predkoscia
        # T = Tacc + Tconst
        print("Time - full")
        T = Tacc + Tcon
    #change dodaj to jako komentarz
    #elif(a == 0)
    #   T = s/lastV
    return T


def MotorCalcS(lastV, vel, t): #float float float
    Tacc = abs((vel-lastV)/MOTOR_ACC_V) #float
    Sacc = (lastV+vel)*0.5*Tacc #float
    Scon = vel*(t-Tacc) #float
    if(t > Tacc):
        return Sacc+Scon # float
    else:
        return Sacc # float


def MotorCalcVel(lastV, s, t): #float float float
    #ale gdy mamy rownierz poruszanie sie z predkoscia stala,
    #to musimy rozwiazac ponizsze rownanie z zalozeniami:
    a = MOTOR_ACC_V #float
    if(lastV*t > s):
        a = -a
    #zakladamy, ze v > lastV
    p = (a*t*t + 2*lastV*t - 2*s)/a
    S = 0 #definicja zmiennej
    if(p < 0): #change
        p = (a*t*t + 2*lastV*t + 2*s)/a
        p = math.sqrt(p)
    if(p>=0):
        p = math.sqrt(p)
        V = lastV - a*p + a*t
        S = MotorCalcS(lastV, V, t)
        if(abs(S - s) > 5):
            print("Vel - minus ")
            V = lastV + a * p + a * t
            if(abs(MotorCalcS(lastV, V, t) - s) > 5):
                print("Vel - Urzyawasz zlych wzorow") #change opcjonalnie mozna by w tym miejscu dodac MOTOR_ERR(MOTOR_ERR_CALC_VEL_2)
    else: # w akcie rozpaczy (gdy nie idzie liczenie tego) - to uprosc
        #obliczenia dobrane metoda doswiadczalna
        #inne opcje to:
        # a) V = s/t //gdy t!=0
        # b) p = math.sqrt(a*t*t + 2*lastV*t + 2*s)/a)
        #    V = lastV + a * p + a * t
        # c) wesola tworczosc
        print("Vel - rozpacz1, t=", t)
        V = lastV + a*t
    return V #change

motors = motors_t();


def MotorGoA(left, right, vel):
    lVl = motors.cmot0 #last vel
    lVr = motors.cmot1
    vel = abs(vel)
    Vl = vel
    Vr = vel
    T = 0.0
    if(left < 0):
        Vl = -vel;
    if(right < 0):
        Vr = - vel
    Tl = MotorCalcTime(lVl, left,  Vl)# last vel from left motor
    print("Tl ", Tl)
    Tr = MotorCalcTime(lVr, right, Vr)# last vel from right mototr
    print("Tr: ", Tr)
    if(Tl > Tr):
        T = Tl
    else:
        T = Tr

    Vl = MotorCalcVel(lVl, left,  T) #change
    Vr = MotorCalcVel(lVr, right, T)
    motors.mot0 = Vl
    motors.mot1 = Vr
    motors.time = T/MOTOR_DRIVER_T


def _stepTo(_from, _to, _step):
    val = _from
    if(_from < _to):
        val = _from + _step
        if(val > _to):
            val = _to
    elif(_from > _to):
        val = _from - _step
        if(val < _to):
            val = _to
    return val


if __name__ == "__main__":
    Vl = [0]
    Vr = [0]
    Sl = [0]
    Sr = [0]
    t  = [0]

    for i in range(0,5):
        left = int(input("lewe kolo: "))
        right = int(input("prawe kolo: "))
        vel = int(input("predkosc: "))
        MotorGoA(left, right, vel);
        print("lewy prawy czas")
        print("predkosc: ", motors.mot0, motors.mot1, float(motors.time), sep=', ');
        while(motors.time > 0):
            motors.cmot0 = _stepTo(motors.cmot0, motors.mot0, MOTOR_DRIVER_T*MOTOR_ACC_V)
            motors.cmot1 = _stepTo(motors.cmot1, motors.mot1, MOTOR_DRIVER_T*MOTOR_ACC_V)
            Vl.append(motors.cmot0)
            Vr.append(motors.cmot1)
            Sl.append(Sl[-1]+Vl[-1]*MOTOR_DRIVER_T)
            Sr.append(Sr[-1]+Vr[-1]*MOTOR_DRIVER_T)
            t.append(t[-1]+1)
            motors.time = motors.time - 1
        print("droga na koniec: ", Sl[-1], Sr[-1], sep=', ');
        print("droga na koniec: ", Sl[-1]*30.28, Sr[-1]*30.28, sep=', ');
        print("\n")
        #wyswietl wyniki
        pl.subplot(2, 1, 1)
        pl.plot(t, Sl)
        pl.plot(t, Sr)
        pl.ylabel('droga')
        pl.subplot(2, 1, 2)
        pl.plot(t, Vl)
        pl.plot(t, Vr)
        pl.ylabel('prędkość')
        pl.show()

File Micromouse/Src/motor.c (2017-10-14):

#include "motor.h"
#include "queue.h"
#include "map.h"

const float 	HALF_WHEELBASE				= (WHEELBASE/2); /* mm*/
const float 	TICKS_PER_MM					= (TICKS_PER_REVOLUTION/(PI*WHEEL_DIAMETER));
const float 	MOTOR_DRIVER_FREQ			= 1000.f; // Hz
const float		MOTOR_DRIVER_T				= 1.f/MOTOR_DRIVER_FREQ;
//const int 		ONE_CELL_DISTANCE			= 5450; // ticks, 180*30,28

// needed for motors
extern TIM_HandleTypeDef MOTOR_HTIM, MOTOR_HTIM_ENC_L, MOTOR_HTIM_ENC_R;
extern uint32_t sens[];


int MotorUpdateStatus(void);
void MotorUpdateEncoder(void);
void MotorUpdateVariable(void);

int abs(int x)
{
	if(x < 0)
		return -x;
	else
		return x;
}



int sgn(int x)
{
	return (x>0)-(x<0);
}

int _roundf(float x)
{
	// zaszumianie
	static float szum = 0;
	szum += 0.013f;
	if(szum > 0.5f)
		szum -= 1.0f;
	x += szum;
	
	// zaokraglanie
	if(x < 0)
		return (int)(x-0.5f);
	else
		return (int)(x+0.5f);
}

//float fast_sqrt(float x)
//{
//	// Heron from Alexandria
//	float p = 0.5f*x;
//	float lastP = x;
//	
//	while(lastP-p > 0.1f)
//	{
//		lastP = p;
//		p = 0.5f*(x/p+p);
//	}
//	
//	return p;
//}


int MotorTruncPWM(float vel)
{
	if(vel >= MOTOR_MAX_PWM)
		return MOTOR_MAX_PWM;
	else if(vel <= -MOTOR_MAX_PWM)
		return -MOTOR_MAX_PWM;
	else
		return vel;
}


void MotorStepResponse(uint16_t PwmL, uint16_t PwmR, uint16_t time)
{
		static uint16_t test_mode = 0;
		uint8_t buf[2];
		uint32_t enc;
			
		if(!test_mode){
			MotorSetPWMRaw(PwmL, PwmR); // make mouse go straight
		}
		if(test_mode > time){
			MotorSetPWMRaw(0, 0);
			HAL_UART_DeInit(&huart1); // stop sending data
		}
			//_itoa(37, aTxBuffer);
		enc = EncL;
		TIM3->CNT = 0;
		buf[0] = enc >> 8;
		buf[1] = enc;
		HAL_UART_Transmit_DMA(&huart1, (uint8_t*)buf, 2);
		test_mode++;
}

void MotorPrintData()
{
		uint8_t buf[2];
		uint32_t enc;
		//_itoa(37, aTxBuffer);
		enc = EncL;
		TIM3->CNT = 0;
		buf[0] = enc >> 8;
		buf[1] = enc;
		HAL_UART_Transmit_DMA(&huart1, (uint8_t*)buf, 2);
}

//========================
//====== VELOCITY ========
//========================

MotorsV motors;
int _motor_flag = 0;
int motor_error = 0;

void MotorReset()
{
	__HAL_TIM_SetCompare(&MOTOR_HTIM, MOTOR_CH_L, 0);
	__HAL_TIM_SetCompare(&MOTOR_HTIM, MOTOR_CH_R, 0);
	EncL = 0;
	EncR = 0;
	memset(&motors.mot[0], 0, sizeof(_MotorV));
	memset(&motors.mot[1], 0, sizeof(_MotorV));
}

void MotorResetEnc()
{
	//m->enc = 0;
	//m->encChange = 0;
	motors.mot[0].lastEnc = 0;
	EncL = 0;
	motors.mot[1].lastEnc = 0;
	EncR = 0;
	//m->idealEnc = 0;
}

void MotorInit()
{
	//todo: turn on timers
	__HAL_TIM_PRESCALER(&MOTOR_HTIM, 7);
	__HAL_TIM_SetAutoreload(&MOTOR_HTIM, MOTOR_MAX_PWM);
	//power 0%
	__HAL_TIM_SetCompare(&MOTOR_HTIM, MOTOR_CH_L, 0);
	__HAL_TIM_SetCompare(&MOTOR_HTIM, MOTOR_CH_R, 0);
	
	// filtracja sygnalu
	//MOTOR_HTIM_ENC_L.Instance->SMCR |= TIM_SMCR_ETF_3;
	//MOTOR_HTIM_ENC_R.Instance->SMCR |= TIM_SMCR_ETF_3;
	
	HAL_TIM_PWM_Start(&MOTOR_HTIM, MOTOR_CH_L);
	HAL_TIM_PWM_Start(&MOTOR_HTIM, MOTOR_CH_R);
	HAL_TIM_Encoder_Start(&MOTOR_HTIM_ENC_L, TIM_CHANNEL_ALL);
	HAL_TIM_Encoder_Start(&MOTOR_HTIM_ENC_R, TIM_CHANNEL_ALL);
	
	MotorReset();
}


void MotorUpdateEnc()
{
	// te zmienne powinny byz liczbami calkowitymi ze znakiem
	// oraz miec taka sama wielkosc jak rejestr przechowujacy
	// impulsy z eknkodera - patrz przejscia CNT przez 0!
	int16_t delta;
	int16_t el = MOTOR_HTIM_ENC_L.Instance->CNT;
	int16_t er = MOTOR_HTIM_ENC_R.Instance->CNT;
	
	delta = el - motors.mot[0].lastEnc;
	motors.mot[0].encChange = delta;
	motors.mot[0].enc += delta;
	
	delta = er - motors.mot[1].lastEnc;
	motors.mot[1].encChange = delta;
	motors.mot[1].enc += delta;
	
	motors.mot[0].lastEnc = el;
	motors.mot[1].lastEnc = er;
	
}

int MotorUpdateStatus()
{
	if(motors.time > 0)
		return 0; // motor running
	else
		return 1; // motor stopped
}



void _MotorUpdateAV(_MotorV* mot)
{
	/// update accelerate and velocity
	/// increase/decrease 'temp' by 'by' to get closer to 'to'
	if(mot->vel < mot->targetVel) // accelerate
	{
		mot->a = MOTOR_ACC_V;
		mot->vel += mot->a*MOTOR_DRIVER_T;
		if(mot->vel > mot->targetVel)
			mot->vel = mot->targetVel;
	}
	else if(mot->vel > mot->targetVel) // deccelerate
	{
		mot->a = -MOTOR_ACC_V;
		mot->vel += mot->a*MOTOR_DRIVER_T;
		if(mot->vel < mot->targetVel)
			mot->vel = mot->targetVel;
	}
	else{ 
		mot->a = 0;
	}
}


void MotorUpdateVariable()
{
	// velocity
	_MotorUpdateAV(&motors.mot[0]);
	_MotorUpdateAV(&motors.mot[1]);
	
	// timing
	if(motors.time > 1) // decrement translation velocity timer
		--motors.time;
	else if(motors.time == 1)
	{
		--motors.time;
		motors.mot[0].targetVel = 0;
		motors.mot[1].targetVel = 0;
		run();
//		int test = (EncL+EncR)/2;
//		_itoa(test, Tx_buf, 10);
//		UI_Send((uint8_t*)Tx_buf);
		// enkodery zerujemy tylko jak robilimsy zakret
//		if(motors.mot[0].idealEnc != motors.mot[1].idealEnc){
//			MotorResetEnc();
//			UI_Send("abc");
//		}
		// resetujemy enkodery po skrecie
		_queue_elem* q_ptr = NULL;
		if(queue.queue_buf[queue.tail].f_ptr == MotorTurnA){
			MotorResetEnc();
			sprintf(Tx_buf, "%d", queue.tail);
			UI_Send((uint8_t*)Tx_buf);
		}
		q_pop(&queue)->f_ptr(queue.queue_buf[queue.tail].a, queue.queue_buf[queue.tail].b, queue.queue_buf[queue.tail].c);
	}
	
	// position
	motors.mot[0].idealEnc += _roundf(motors.mot[0].vel*MOTOR_DRIVER_T*TICKS_PER_MM);
	motors.mot[1].idealEnc += _roundf(motors.mot[1].vel*MOTOR_DRIVER_T*TICKS_PER_MM);
}

float Kp = 2.f, Ki = 0.01f, Kd = 0.01f;
void MotorDriver()
{
	int err;
	for(int i = 0; i < 2; ++i)
	{
		// oblicz uchyba jako roznice pomiedzy pozycja idelana i ta rzeczywista
		err = motors.mot[i].idealEnc - motors.mot[i].enc;
		motors.mot[i].errD = err - motors.mot[i].errP;
		motors.mot[i].errI+= err;
		motors.mot[i].errP = err;
		
		// nasycenie czlonu I
		const int errIMax = 1200;
		if(motors.mot[i].errI > errIMax)
			motors.mot[i].errI = errIMax;
		else if(motors.mot[i].errI < -errIMax)
			motors.mot[i].errI = -errIMax;
		
//		// sprzezenie od bledu pozycji
//		motors.mot[i].PWM = (int)(Kp*((float)(motors.mot[i].errP) // 500
//														+ Ki*(float)(motors.mot[i].errI) // 1000
//														+ Kd*(float)(motors.mot[i].errD))); // 56
//		// sprzezenie od zadanej predkosci
//		motors.mot[i].PWM += (int)(0.17f*(motors.mot[i].vel
//														+ 0.3f*motors.mot[i].a)); // 0.03
	}
	
	
	int errVP = motors.mot[0].errP + motors.mot[1].errP;
	int errVD = motors.mot[0].errD + motors.mot[1].errD;
	int errWP = motors.mot[0].errP - motors.mot[1].errP;
	int errWD = motors.mot[0].errD - motors.mot[1].errD;
	
	int errV = errVP + 5*errVD;
	int errW = errWP + 5*errWD;
	 
	// sprzezenie od czujnikow
	// tylko gdy gdzies jedziesz
	static int i = 0;
	if(motors.time > 0 && ++i > 2)
	{
		i = 0;
		if(_motor_flag & FLAG_SENSOR)
		{
			int sF = SensorFeedback();
			motors.mot[0].idealEnc += sF;
			motors.mot[1].idealEnc -= sF;
		}
	}
	
	motors.mot[0].PWM = errV + errW;
	motors.mot[1].PWM = errV - errW;
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

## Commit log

2015-11-28 dodalem schemat z jednym golpinem i biblioteke z enkoderem
    [main.brd, main.sch]
2015-12-01 bibloteki, szkic i plytka glowna
    [Drawing1.dwg, MM_Main.sch]
2015-12-03 bilbiotek od mm, zeby nie dodawac za kazdym razem Eagle->use
    [MM_Main.sch]
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2015-12-05 dodanie tranzystorow do diod
    [MM_Main.sch]
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2015-12-12 poprawka do diod i stabilizatora
    [MM_Main.sch]
2015-12-18 gitignore i sch
    [MM_Main.sch, MM_Main_new.sch, MM_Main_old.sch]
2015-12-18 main.brd deleted online with Bitbucket
    [main.brd]
2015-12-18 main.sch deleted online with Bitbucket
    [main.sch]
2016-01-01 dodanie stm32f4 do lib
    [Drawing1.dwg, MM_Main.sch]
2016-01-03 gyro na master
    [gyro.brd, gyro.sch]
2016-01-03 INT_A i dopasowanie goldpinow
    [gyro.brd, gyro.sch]
2016-01-04 enkodery w bibliotece
    [encoder.brd, encoder.sch]
2016-01-04 pcb do enkoderow i poprawione lbr
    [encoder.brd, encoder.sch]
2016-01-05 dodanie wymiarowania do gyro i zepsucie termali :P
    [MM_Main.sch, gyro.brd, gyro.sch]
2016-01-05 drobna aktualizacja
    [MM_Main.sch, gyro.brd]
2016-01-05 gora jest juz prawie gotowa, trzeba jeszcze rozmiescic kondensatory
    [MM_Main.brd]
2016-01-05 poprawilem poligon w gryo
    [gyro.brd]
2016-01-05 dodany buzzer w lbr i sch
    [MM_Main.sch]
2016-01-06 wszystkie sciezki polaczone \!
    [MM_Main.brd, MM_Main.sch]
2016-01-06 czesciowy DRC
    [MM_Main.brd]
2016-01-09 renament - 4 LED + all on top
    [MM_Main.brd, MM_Main.sch]
2016-01-09 rozwoj brd
    [MM_Main.brd, MM_Main.sch]
2016-01-09 aktualizacja brd
    [MM_Main.brd, MM_Main.sch]
2016-01-10 brd prawie gotowe
    [MM_Main.brd, MM_Main.sch]
2016-01-10 wszystko polaczone, trzeba dopiscic
    [MM_Main.brd, MM_Main.sch]
2016-01-12 poprawilem zasilanie, rx/tx, obudowa stmki
    [MM_Main.brd, MM_Main.sch]
2016-01-12 dodalem stm32f4 do biblioteki
    [MM_Main.brd, MM_Main.sch]
2016-01-14 nowe gniazdo do zas
    [MM_Main.brd, MM_Main.sch]
2016-01-15 dodalem adxrs620
    [MM_Main.brd, MM_Main.sch]
2016-01-15 gyro gotowe! w lbr pozmieniane poligony
    [gyro.brd, gyro.sch]
2016-01-16 zmiana gniazda zasilania, VCC i VSS
    [MM_Main.brd, MM_Main.sch]
2016-01-16 no male dodatki
    [MM_Main.brd, MM_Main.sch]
2016-01-18 rozwoj pcb
    [MM_Main.brd]
2016-01-18 poczatek 6LED -- dlugi przod
    [MM_Main.brd, MM_Main.sch]
2016-01-20 zmieniony przod i kolejnosc ledow
    [MM_Main.brd, MM_Main.sch]
2016-01-20 drobna zmiana przy laczeniu masy i leda
    [MM_Main.brd]
2016-01-20 gerbery do gyro
    [gyro.brd, gyro.sch]
2016-01-21 6 diod
    [MM_Main.brd, MM_Main.sch]
2016-01-21 6LED pcd prawie pusty przod
    [MM_Main.brd, MM_Main.sch]
2016-01-21 wszystko polaczone, zmiana w gyro z vcc na +3v3
    [MM_Main.brd, gyro.brd]
2016-01-23 taki rozstaw diod?
    [MM_Main.brd]
2016-01-23 2 zwykle ledy z przodu
    [MM_Main.brd, MM_Main.sch]
2016-01-23 dopasowanie dimension, dodanie otworow i radiatorow, DRC
    [MM_Main.brd]
2016-01-24 drc, kosmetyka, opisy, pasztet
    [MM_Main.brd, MM_Main.sch]
2016-01-25 poprawa bledow, dodanie rezystorow na wyjsciach stm-glownie w modolach, poprawa elementu 9axis z biblioteki
    [MM_Main.brd, MM_Main.sch, encoder.brd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]
2016-01-26 dodany napis
    [MM_Main.brd]
2016-01-28 drobna zmiana switch'y
    [MM_Main.brd, MM_Main.sch]
2016-01-28 w poprzednim jest maly blad
    [MM_Main.brd]
2016-01-29 poprawilem przelotki i ustawilem napisy
    [MM_Main.brd, gyro.brd]
2016-01-29 poprawki warst opisowych, dodanie gerberow mm
    [MM_Main.brd, MM_Main.sch]
2016-01-31 male zmiany
    [MM_Main.brd]
2016-01-31 jeszcze mniejsze zmiany
    [gyro.brd]
2016-01-31 nazwy diod teraz do siebie pasuja
    [MM_Main.brd, MM_Main.sch]
2016-02-02 zamiana warstw
    [MM_Main.brd, MM_Main.sch, big.brd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]
2016-02-09 schamat kodu z CubeMX
    [MM_Main.sch, big.brd]
2016-02-12 poprawione przyciski, kwarc i wylacznik zasilania
    [MM_Main.brd, MM_Main.sch]
2016-02-12 PD2 zamienione z PA15
    [MM_Main.brd, MM_Main.sch]
2016-02-12 dodany suwak i miejsce na 2 lipo
    [MM_Main.brd, MM_Main.sch]
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2016-02-13 to 2 gniazdo moze szorowac o kolo... zmienilem tez konfiguuracje power-switcha, bo tak patrzac na strone electro-parku to tak odczyruje ta konfiguracje, zrobilem drc
    [MM_Main.brd, MM_Main.sch]
2016-02-14 drobne poprawki, chyba koniec :P
    [MM_Main.brd]
2016-02-18 wywalilem elementy ktore byly pod podstawka silnika
    [MM_Main.brd, MM_Main.sch]
2016-02-24 poprawione piny w cubemx
    [MM_Main.brd, MM_Main.sch]
2016-02-24 cubemx+ nowe gerbery
    [MM_Main.brd]
2016-02-27 gerbery z flaga i bez flagi, dodalem te dziurki na koncu
    [MM_Main.brd]
2016-02-28 wieksze otwory dla buzzera
    [MM_Main.brd, MM_Main.sch]
2016-02-28 projekt w Keil + motor.c
    [MM_Main.sch]
2016-03-24 Nowy projekt keil
    [MM_Main.brd, MM_Main.sch]
2016-04-03 UI start
    [MM_Main.brd, MM_Main.sch]
2016-04-13 Beep, BeepInit LedInit...
    [MM_Main.brd]
2016-04-26 porzadki i jeden kod
    [MM_Main.brd, MM_Main.sch, big.brd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]
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2016-09-30 buzzer wielowatkowy, pozadkowanie kodu w motorze
    [UI.c, UI.h, main.c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]
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2016-10-12 poprawilem enkodery
    [encoder.brd, encoder.sch]
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2016-10-25 naprawa resetu enkoderow, zmiana definicji SENS_XX na sens[x] a nie sensor[x].sens, dodanie wyswietlania nastaw, zmiana wskaznika zwracanego przez _ftoa i itoa na ostatni, a nie pierwszy element
    [UI.c, main.c, motor.c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]
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2016-11-18 dodane modele kol i podstawki silnikow
    [spacer.stl, wheel.ipt]
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

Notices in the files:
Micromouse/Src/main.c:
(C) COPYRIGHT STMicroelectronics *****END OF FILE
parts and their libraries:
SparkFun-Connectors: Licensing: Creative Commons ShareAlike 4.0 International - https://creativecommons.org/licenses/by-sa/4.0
